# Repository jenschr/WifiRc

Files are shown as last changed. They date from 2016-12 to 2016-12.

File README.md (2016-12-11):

#Wifi RC project
A simple board to make RC projects from. Has three simple motor controllers, 6 prewired LED connections, SPI and Serial outputs & more.

Can run off USB (no motor) or 7.4 or 11.1V batteries (depending on what your motors need). Set your power source using the VS jumper. The 5V outputs are intended to dirve Servo's, but the wiring isn't exactly ideal. A new version may set aside 3 pins for dedicated Servo outputs.

The module has been produced and tested, but not yet mounted in a model. See pictures of the reflowed and soldered board [here](http://jcprojects.tumblr.com/post/149121660034/my-second-dev-board-based-on-the-particleio-p1) and a short video from testing [here](http://jcprojects.tumblr.com/post/154342641139/so-much-blink-all-pins-mapped-out-and-tested-i).

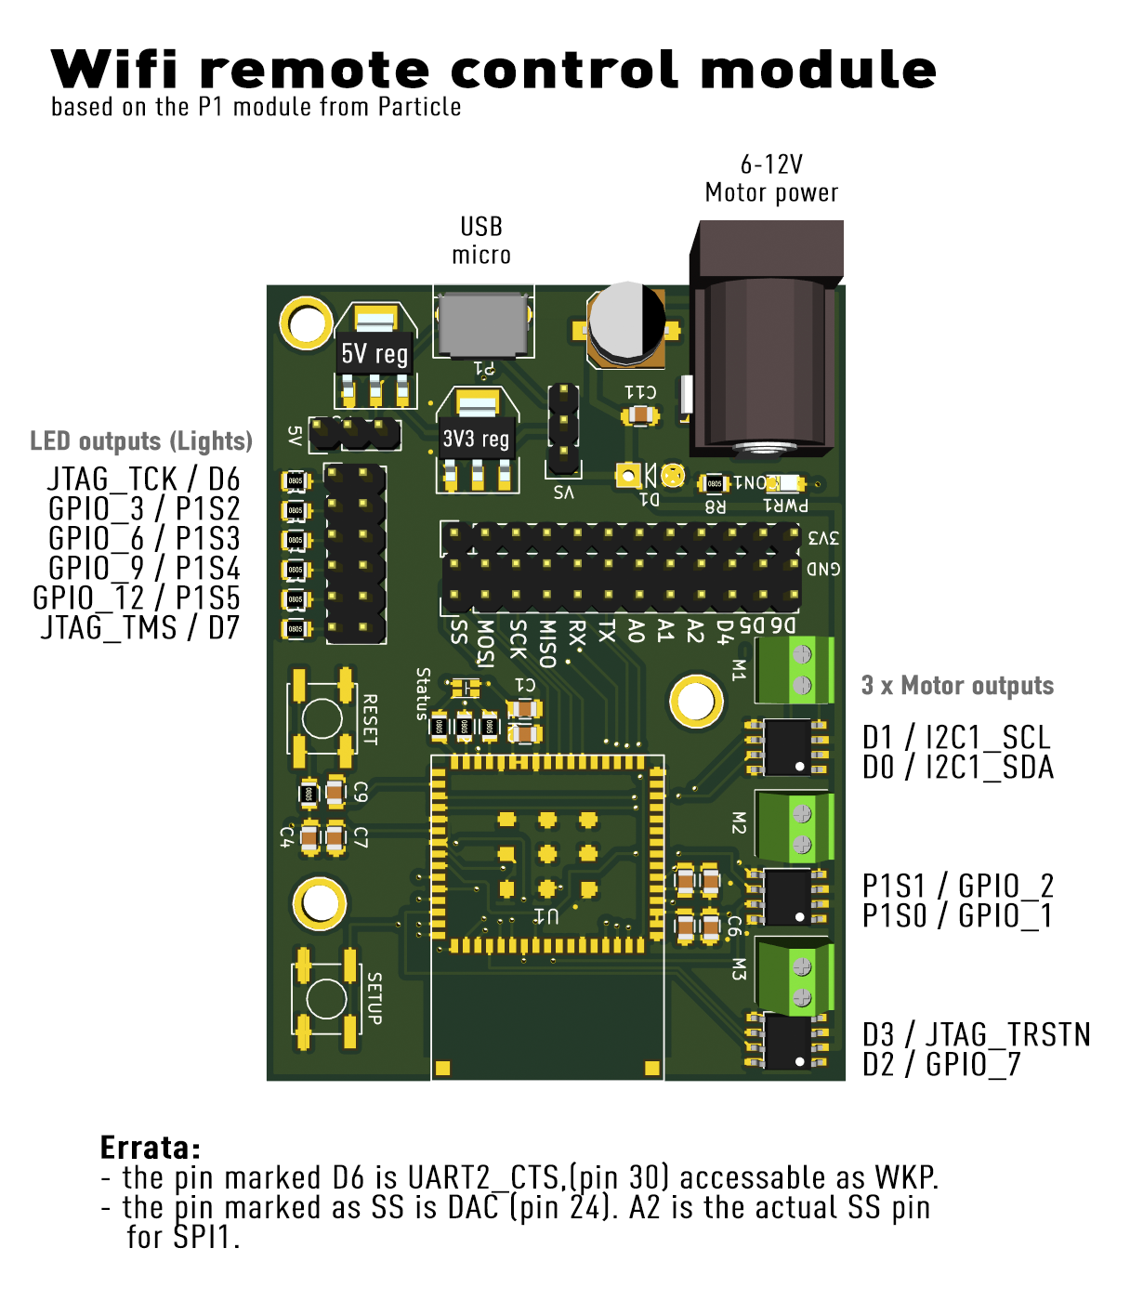
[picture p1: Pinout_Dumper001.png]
Pinout


##BOM
The [bill of materials](/Dumper001/Dumper001.csv) can be found as a .csv file in this repository. The core part is the P1 module (USI WM-N-BM-14) that you can pick up in a [10-pack from the Particle store](https://store.particle.io/products/p1), pre-flashed with the Particle firmware ([P1 datasheet/docs](https://docs.particle.io/datasheets/p1-datasheet/)).

I have used AMS1117 for both 3.3 and 5V regulation and that seems to work well without any signs of overheating. The L9110 motor drivers are weak, but will do the trick for small motors.

##Errata
* The pin marked D6 is UART2_CTS,(pin 30) accessable as WKP.
* The pin marked as SS is DAC (pin 24). A2 is the actual SS pin for SPI1.

Both of these pins work for digital IO, but use the constant WKP to access the D6 pin and DAC to access the pin marked SS.

##License
[CERN OHL V1.2](http://www.ohwr.org/licenses/cern-ohl/v1.2)

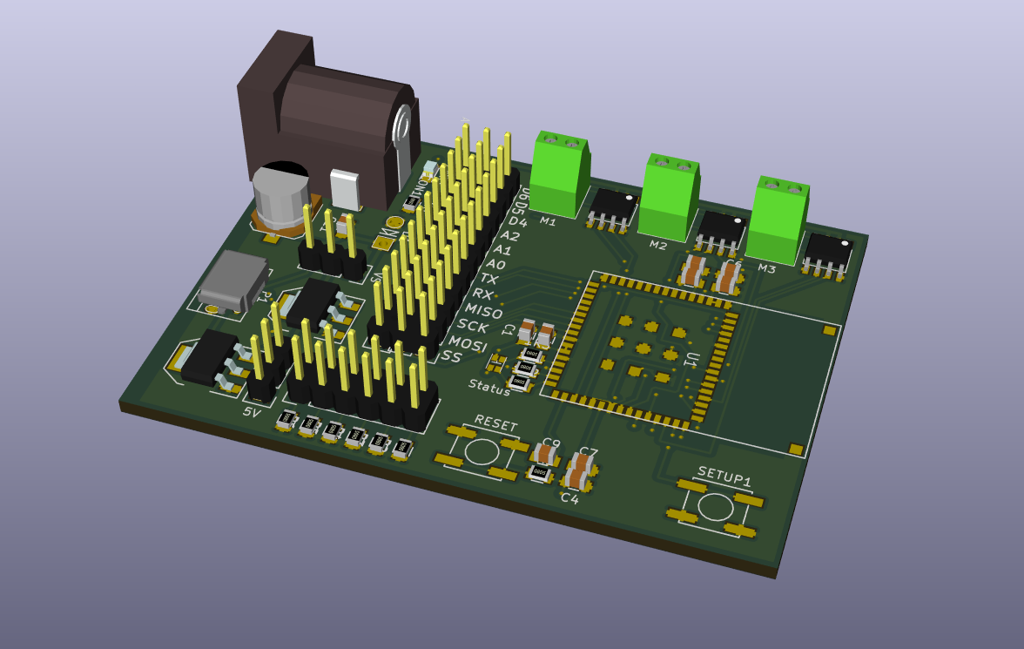
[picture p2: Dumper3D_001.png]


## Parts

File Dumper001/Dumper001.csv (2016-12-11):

Id | Designator | Package | Quantity | Designation | Supplier and ref
1 | REF**,REF**,REF** | 1pin | 3 | 1pin
2 | 1K1,1K2,1K3 | R_0805 | 3 | 1k
3 | C1,C3,C6,C7,C9,C11 | C_0805 | 6 | 0.1uf
4 | C2,C4,C5,C8 | C_0805 | 4 | 10uf
5 | P1 | USB_Micro-B | 1 | USB_OTG
6 | R1 | R_0805 | 1 | 10k
7 | RESET,SETUP1 | SW_SPST_EVPBF | 2 | SW_PUSH
8 | U1 | WM-N-BM-14 | 1 | WM-N-BM-14
9 | U2 | SOT-223 | 1 | AMS1117 3.3V
10 | GND | Pin_Header_Straight_2x12 | 1 | CONN_02X12
11 | C10 | c_elec_6.3x5.7 | 1 | 47uf
12 | P3 | Pin_Header_Straight_2x06 | 1 | LedConnector
13 | VS,5V | Pin_Header_Straight_1x03 | 2 | CONN_01X03
14 | 3V3 | Pin_Header_Straight_1x12 | 1 | CONN_01X12
15 | R2,R3,R4,R5,R6,R7 | R_0805 | 6 | 470R
16 | Status | 0605_RGB_LED | 1 | RGB_LED
17 | U4,U5,U6 | so-8 | 3 | L9110
18 | R8 | R_0805 | 1 | 1000R
19 | M2 | TerminalBlock_Pheonix_MPT-2.54mm_2pol | 1 | M2
20 | M3 | TerminalBlock_Pheonix_MPT-2.54mm_2pol | 1 | M3
21 | CON1 | BARREL_JACK | 1 | BARREL_JACK
22 | PWR1 | LED_0805 | 1 | LED
23 | M1 | TerminalBlock_Pheonix_MPT-2.54mm_2pol | 1 | M1
24 | D1 | Diode_DO-41_SOD81_Vertical_AnodeUp | 1 | InDiode
25 | U7 | SOT-223 | 1 | AMS1117 5.0V

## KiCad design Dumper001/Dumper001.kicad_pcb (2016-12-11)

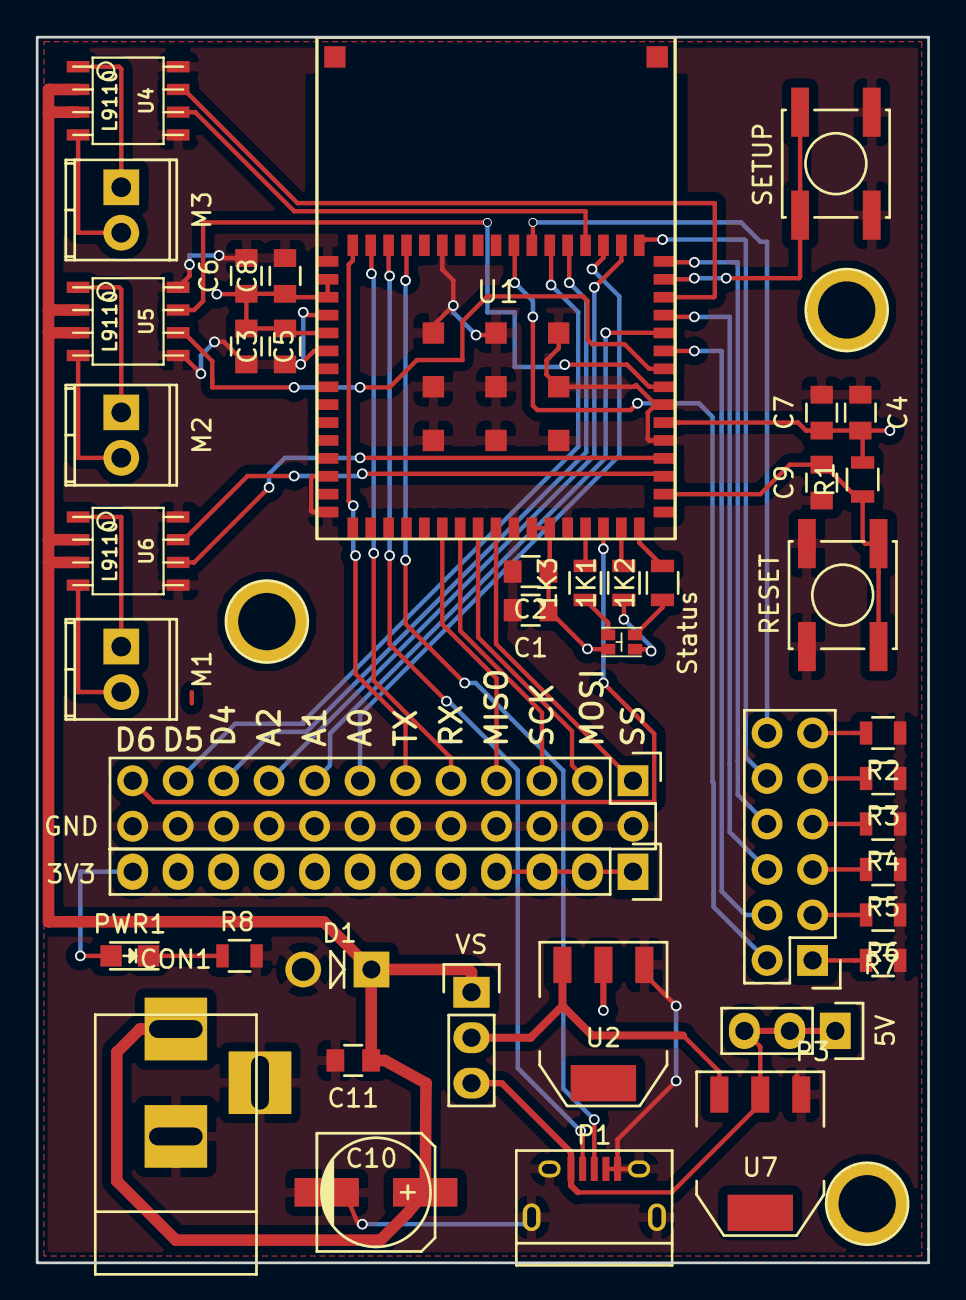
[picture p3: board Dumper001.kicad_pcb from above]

Board: 2 copper layers, 49.8 x 68.5 mm, 43 parts (0 on the bottom side), 52 nets.

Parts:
1K1, 1K2, 1K3: 1k; R_0805
3V3: CONN_01X12; Pin_Header_Straight_1x12
5V: CONN_01X03; Pin_Header_Straight_1x03
C1, C3, C6, C7, C9, C11: 0.1uf; C_0805
C2, C4, C5, C8: 10uf; C_0805
C10: 47uf; c_elec_6.3x5.7
CON1: BARREL_JACK
D1: InDiode; Diode_DO-41_SOD81_Vertical_AnodeUp
GND: CONN_02X12; Pin_Header_Straight_2x12
M1: M1; TerminalBlock_Pheonix_MPT-2.54mm_2pol
M2: M2; TerminalBlock_Pheonix_MPT-2.54mm_2pol
M3: M3; TerminalBlock_Pheonix_MPT-2.54mm_2pol
P1: USB_OTG; USB_Micro-B
P3: LedConnector; Pin_Header_Straight_2x06
PWR1: LED; LED_0805
R1: 10k; R_0805
R2, R3, R4, R5, R6, R7: 470R; R_0805
R8: 1000R; R_0805
RESET: SW_PUSH; SW_SPST_EVPBF
SETUP: SW_PUSH; SW_SPST_EVPBF
Status: RGB_LED; 0605_RGB_LED
U1: WM-N-BM-14
U2: AMS1117 3.3V; SOT-223
U4, U5, U6: L9110; so-8
U7: AMS1117 5.0V; SOT-223
VS: CONN_01X03; Pin_Header_Straight_1x03

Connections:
+3V3: 3V3.1, 3V3.2, 3V3.3, 3V3.4, 3V3.5, 3V3.6, 3V3.7, 3V3.8, 3V3.9, 3V3.10, 3V3.11, 3V3.12, C1.1, C2.1, C3.2, C4.2, C5.1, C6.1, C7.1, C8.1, PWR1.2, R1.2, Status.1, U1.2, U1.3, U1.5, U1.26, U1.27, U1.38, U2.2
+5V: 5V.1, 5V.2, 5V.3, P1.1, U7.2, VS.3
+12V: C10.1, C11.1, CON1.1, D1.1, U4.2, U4.3, U5.2, U5.3, U6.2, U6.3, VS.1
GND: C1.2, C2.2, C3.1, C4.1, C5.2, C6.2, C7.2, C8.2, C9.1, C10.2, C11.2, CON1.2, CON1.3, D1.2, GND.2, GND.4, GND.6, GND.8, GND.10, GND.12, GND.14, GND.16, GND.18, GND.20, GND.22, GND.24, P1.4, P1.5, P1.6, R2.1, R3.1, R4.1, R5.1, R6.1, R7.1, R8.1, RESET.1, SETUP.1, U1.1, U1.4, U1.6, U1.13, U1.15, U1.25, U1.28, U1.37, U1.39, U1.59, U1.65, U1.66, U1.67, U1.68, U1.69, U1.70, U1.71, U1.72, U1.73, U2.1, U4.5, U4.8, U5.5, U5.8, U6.5, U6.8, U7.1
GPIO_A0: GND.13, U1.50
GPIO_A1: GND.15, U1.43
GPIO_A2: GND.17, U1.49
GPIO_D4: GND.19, U1.52
GPIO_D5: GND.21, U1.53
GPIO_D6: GND.23, U1.30
LED1: P3.2, U1.55
LED2: P3.4, U1.42
LED3: P3.6, U1.44
LED4: P3.8, U1.47
LED5: P3.10, U1.48
LED6: P3.12, U1.54
M1a: M1.1, U6.1
M1b: M1.2, U6.4
M2a: M2.1, U5.1
M2b: M2.2, U5.4
M3a: M3.1, U4.1
M3b: M3.2, U4.4
MISO: GND.7, U1.21
MOSI: GND.3, U1.23
unnamed: 1K1.1, Status.4
unnamed: 1K1.2, U1.31
unnamed: 1K2.1, Status.3
unnamed: 1K2.2, U1.32
unnamed: 1K3.1, Status.2
unnamed: 1K3.2, U1.29
unnamed: P3.1, R7.2
unnamed: P3.3, R6.2
unnamed: P3.5, R5.2
unnamed: P3.7, R4.2
unnamed: P3.9, R3.2
unnamed: P3.11, R2.2
unnamed: U2.3, U7.3, VS.2
unnamed: PWR1.1, R8.2
unnamed: U1.35, U6.7
unnamed: U1.36, U6.6
unnamed: U1.40, U5.7
unnamed: U1.41, U5.6
unnamed: U1.45, U4.7
unnamed: U1.51, U4.6
RESET: C9.2, R1.1, RESET.2, U1.34
RX: GND.9, U1.63
SCK: GND.5, U1.22
SETUP: SETUP.2, U1.46
SS: GND.1, U1.24
TX: GND.11, U1.64
USBD+: P1.3, U1.61
USBD-: P1.2, U1.62
